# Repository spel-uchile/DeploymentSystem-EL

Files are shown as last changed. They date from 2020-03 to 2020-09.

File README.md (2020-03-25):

# DeploymentSystem-EL
Proyecto de curso EL. Diseño de sistema de despliegue

#### Parte eléctrica
 - Diseñar una nueva placa con un micro más pequeño y utilizando el espacio en los InterStage.
 - Revisar documentacion de Pinout de Stack (https://docs.google.com/spreadsheets/d/16q0HoTVAfZYG_5lE80G09ZOd-HxBMbC0y2KJIxqkWWU/edit#gid=0).
 - Instrucciones con comandos. 
 
#### Parte Mecánica
 - Revisar articulaciones en CAD (Carpeta general de CAD: https://drive.google.com/drive/u/0/folders/1X1Ea6DyqA-4cPEp2hvyv38Jz5EprBwpk).
   "NO MODIFICAR DIRECTAMENTE"
 - Leer CubesatRev 13 especificaciones de diseños (Tolerancias de diseños, dimensiones maximas de extrucción, estandar de dimensión). https://www.cubesat.org/resources.
 - Exportar las caras de los InterStage a DXF para el diseño del Board.
 - Crear articulaciones en los paneles.

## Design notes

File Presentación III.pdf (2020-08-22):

# SPEL: Deployment System

Alumnos: | Diego Benavides
| Javiera Chasco
Profesor Guía: | Elías Obreque

EL4030-1: Seminario de Diseño e Innovación
Facultad de Ciencias Físicas y Matemáticas, Universidad de Chile

# Agenda

- Presentación del problema.
- Tareas asignadas.
- Labores realizadas.
- Estado actual.
- Aprendizajes y próximos pasos.

# Presentación del problema

- La meta del presente trabajo es lograr implementar un circuito eléctrico que sea capaz de activar un sistema de despliegue de los paneles de protección lumínica y radiación del nanosatèlite PlantSat.
- Para ello, se le hace entrega al equipo de trabajo un circuito base que ya es capaz de realizar dicha acción, el cual se puede apreciar en la figura 1.

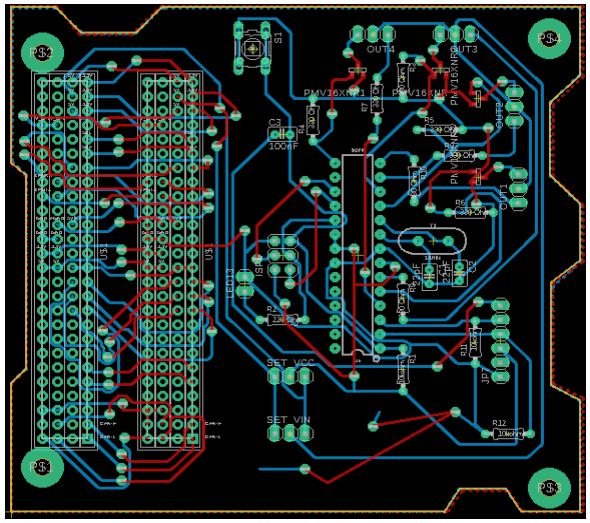
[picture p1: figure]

Figura 1: Placa original del sistema de despliegue.

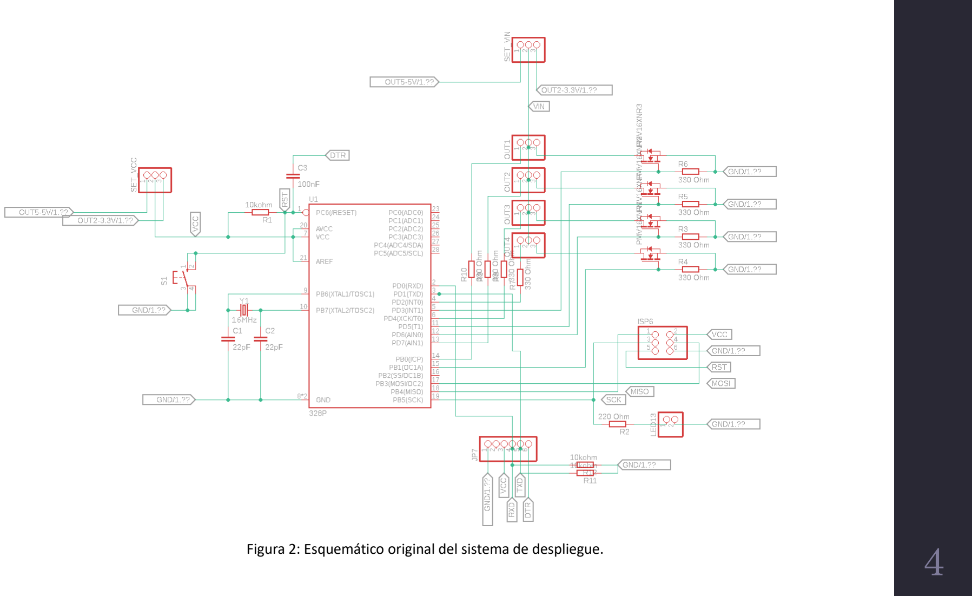
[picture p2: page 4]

Figura 2: Esquemático original del sistema de despliegue.

# Tareas eléctricas designadas

- Realizar una división del circuito original en cuatro subcircuitos.
- Definir un esquema de interconexión entre los subcircuitos y el protocolo de comunicación.
- Buscar o confeccionar componentes SMD para todos los componentes eléctricos del circuito base.
- Rutear los subcircuitos de acuerdo a los estándares de fabricación y recomendaciones de miembros del laboratorio con experiencia previa.
- Revisión y depuración de los esquemáticos y boards para cotizar la fabricación de estos.
- Programar Instrucciones para el funcionamiento de los circuitos.

# Tareas mecánicas asignadas

- Familiarizarse con las especificaciones de diseño descritas en CubesatRev 13.
- Crear soporte para los paneles de despliegue.
- Apoyar en las labores de diseño del esquemático y del board.
- Modificar las placas según necesidad de diseño.
- Crear soporte para montar una cámara en la estructura principal del nanosatélite.

# Especificaciones de diseño del CubeSat

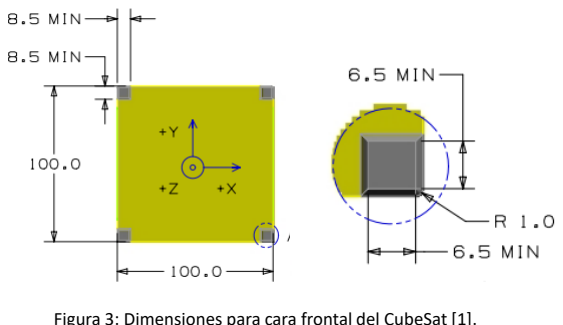
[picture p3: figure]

Figura 3: Dimensiones para cara frontal del CubeSat [1].

Para un CubeSat3U:

- Para la estructura se sugiere utilizar 4 aleaciones de aluminio.
- La masa no debe superar los 4 kg.
- Sus dimensiones deben ser 10x10x34.5 cm³
- Ningún componente puede exceder los 6.5 mm normal a la superficie.
- La tolerancia es ±0.1.

# Especificaciones de diseño del CubeSat

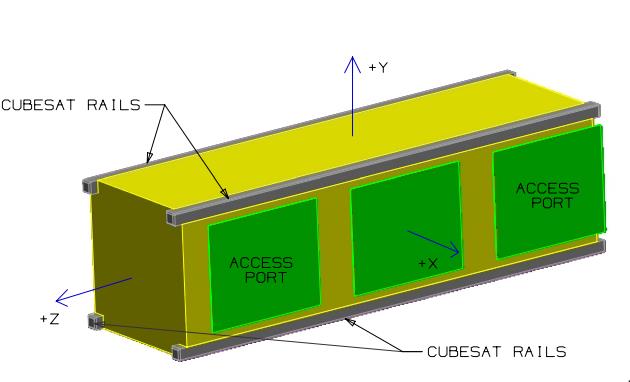
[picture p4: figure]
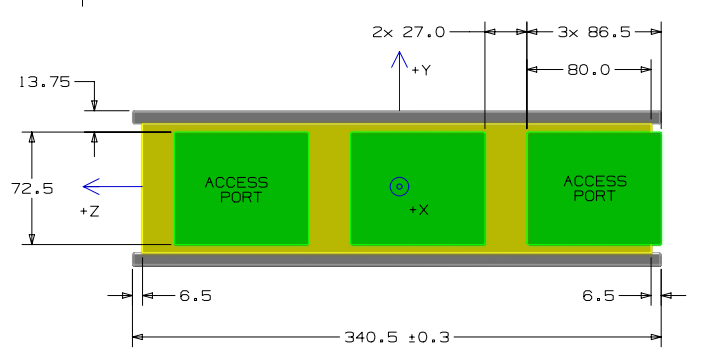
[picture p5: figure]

Figura 4: Dimensiones para cara lateral y vista completa del CubeSat [1].

# Especificaciones de diseño de las PCB

Interstage tipo A

Figura 5: Dimensiones interstage tipo A.

# Especificaciones de diseño de las PCB

Interstage tipo B1

10 Figura 6: Dimensiones interstage tipo B1.

# Especificaciones de diseño de las PCB

Interstage tipo B2

11 Figura 7: Dimensiones interstage tipo B2.

# Especificaciones de diseño de las PCB

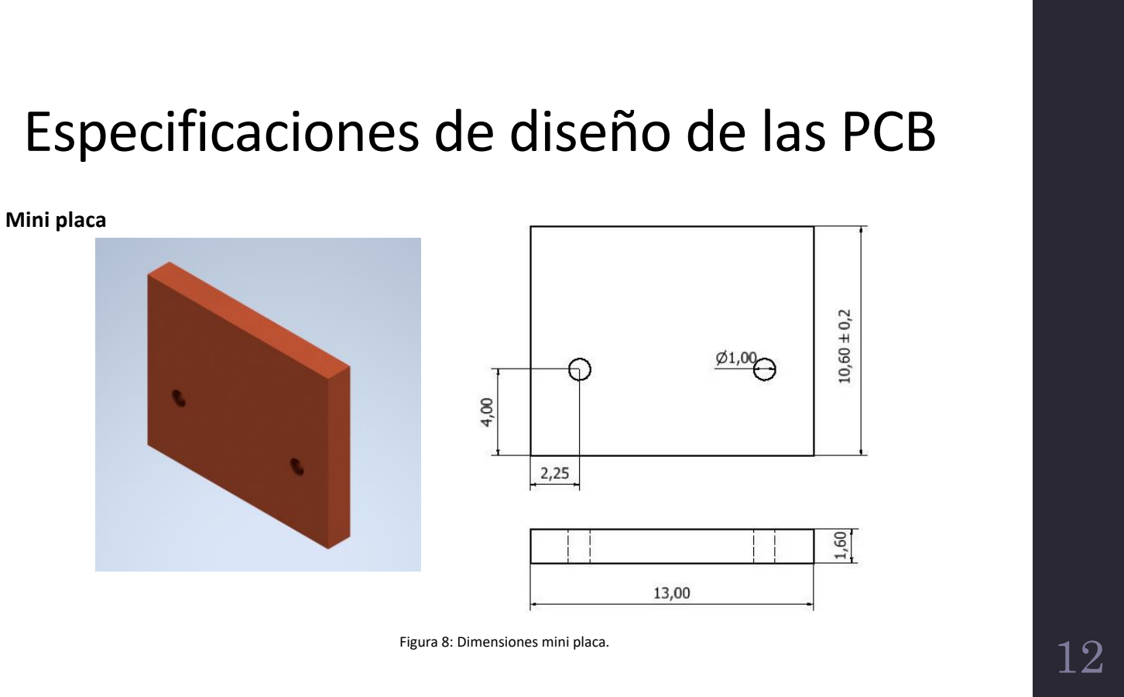
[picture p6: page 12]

Mini placa

12 Figura 8: Dimensiones mini placa.

# Soporte para paneles de despliegue

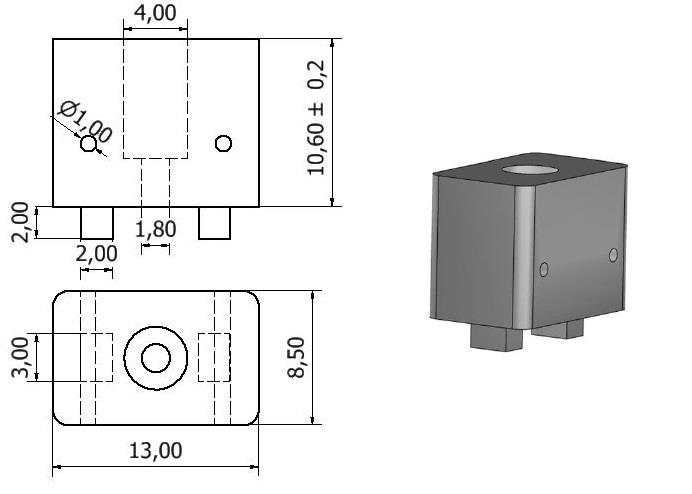
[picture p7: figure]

13 Figura 9: Dimensiones soporte para paneles solares.

# Soporte para cámara

- Se desea diseñar un soporte para un módulo de cámara Raspberry Pi V2.
- El soporte debe ocupar el espacio libre en la estructura, tratando de ser lo menos invasivo posible.

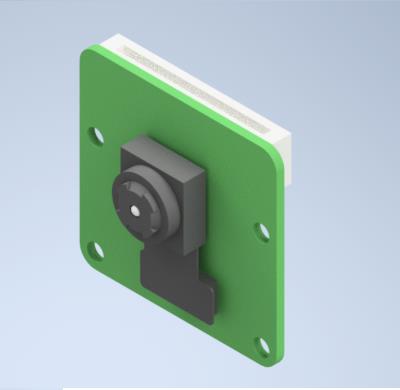
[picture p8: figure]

Figura 10 : Módulo de cámara Raspberry Pi V2.

# Soporte para cámara

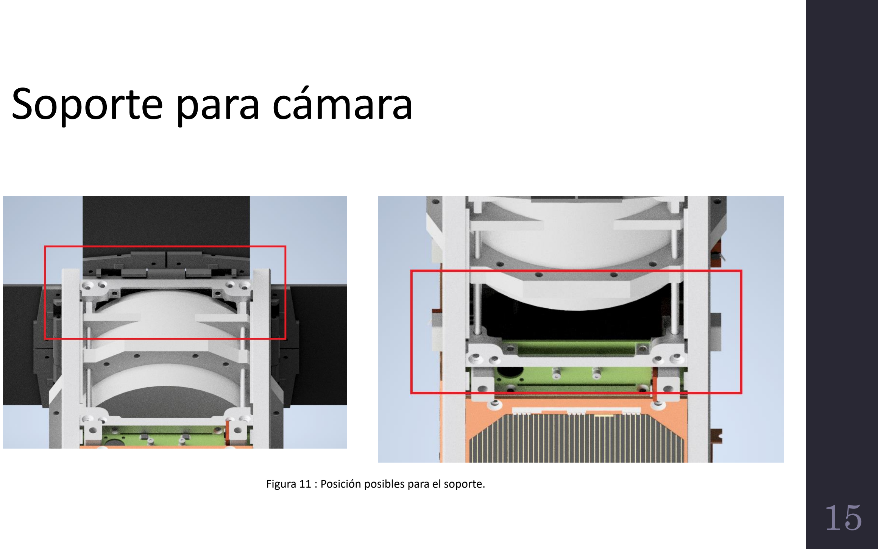
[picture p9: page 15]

Figura 11 : Posición posibles para el soporte.

# Soporte para cámara

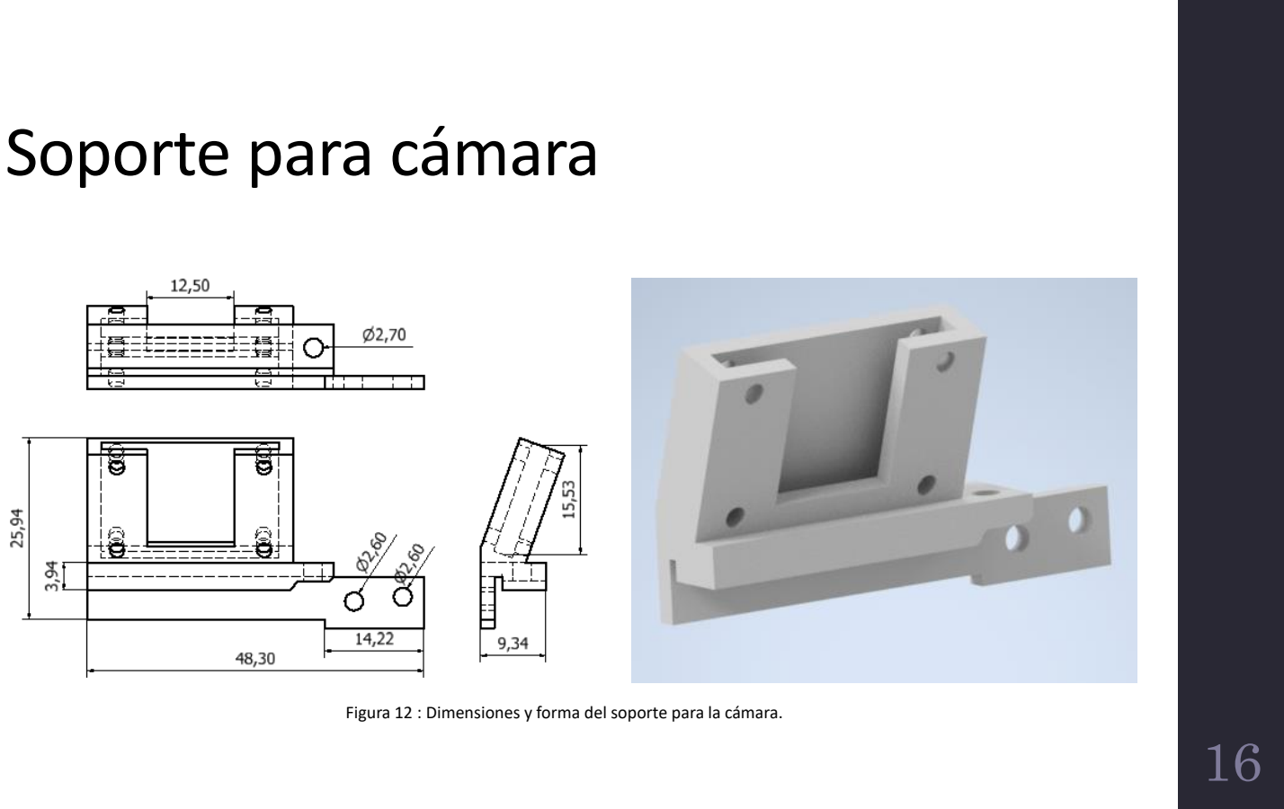
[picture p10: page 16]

Figura 12 : Dimensiones y forma del soporte para la cámara.

# Soporte para cámara

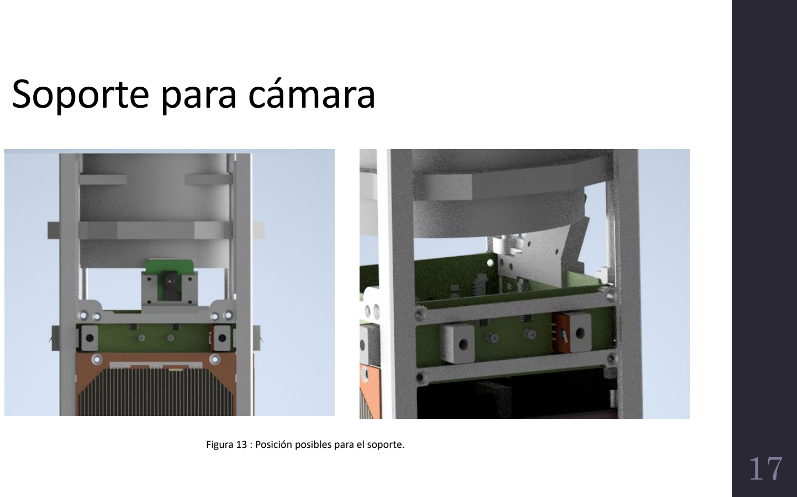
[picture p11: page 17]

Figura 13 : Posición posibles para el soporte.

# Ubicación de las placas

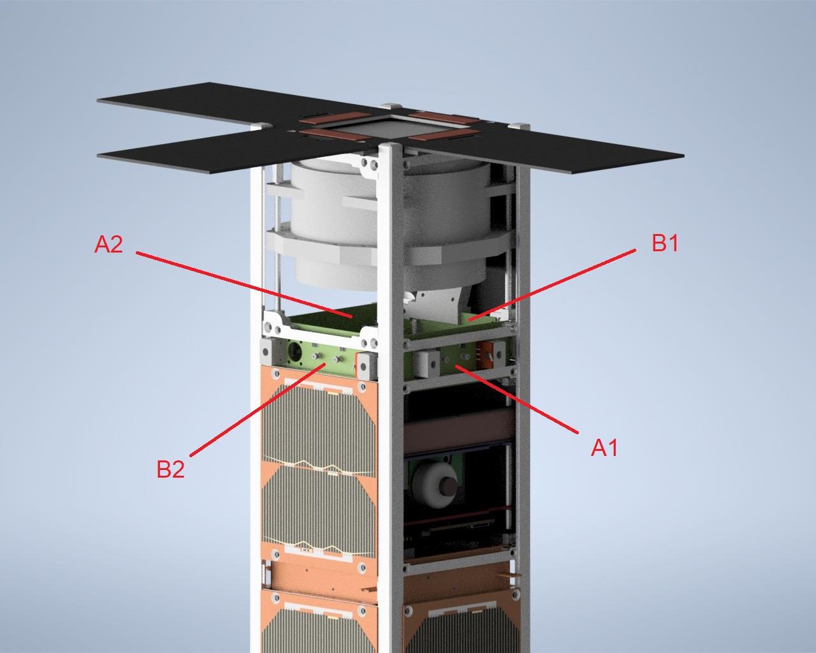
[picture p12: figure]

18 Figura 14: Vista 3D de PlantSat

# Esquema de conexión eléctrica propuesto

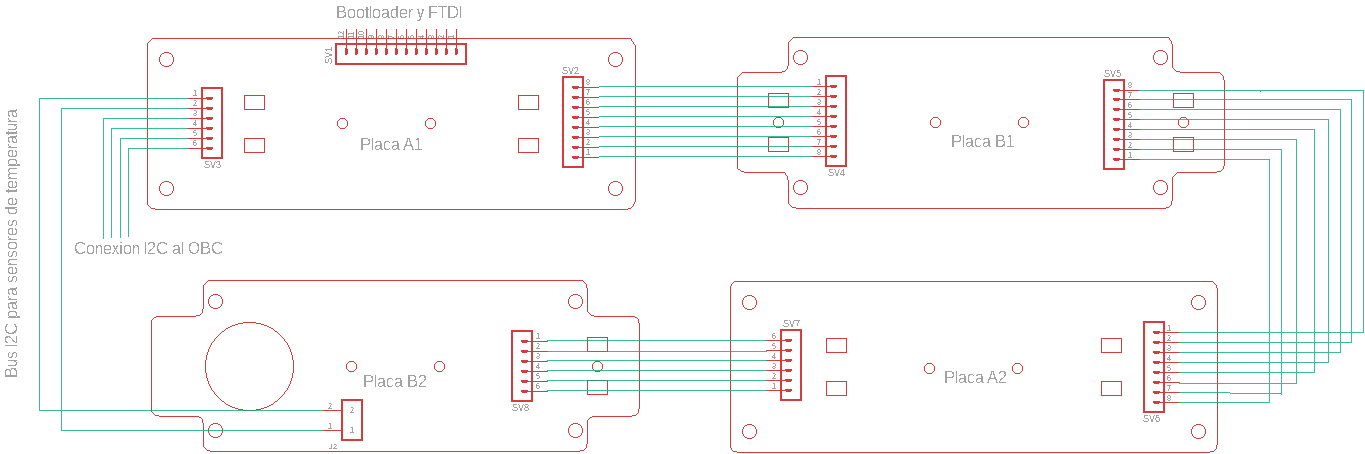
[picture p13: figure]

19 Figura 15: Esquemàtico general del circuito propuesto.

# Esquema de conexión eléctrica propuesto

Placa principal: A1

- Corresponde a la placa central del sistema de despliegue, pues de este lugar se envían desde el microcontrolador (ATmega 328p) las ordenes de activación del sistema de despliegue para cada placa, y donde también se procesan las lecturas de medición de temperatura de estas. Por simplicidad, tanto la placa como los dispositivos que se encuentran ubicados en ella son alimentados con un voltaje continuo de 5V.
- Cuenta con un microcontrolador, dos sensores de temperatura, un interruptor de contacto, y el mosfet para activar el sistema de despliegue de un panel.

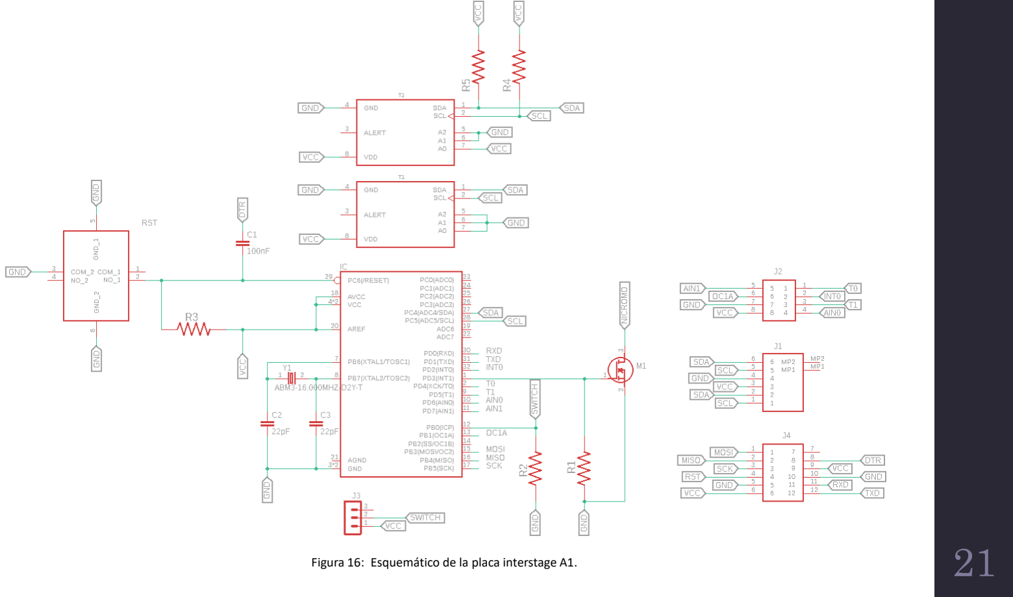
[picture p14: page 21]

Figura 16: Esquemático de la placa interstage A1. | 21

# Esquema de conexión eléctrica propuesto

Placas secundarias: B1, A2 y B2

- Son placas que reciben ordenes desde la principal, son capaces de activar el sistema de despliegue de sus paneles asociados y de registrar la temperatura fuera del satelite.
- A diferencia de la principal, cada una de ellas está compuesta por dos sensores de temperatura, un interruptor de contacto, y un mosfet para activar el sistema de despliegue de un panel.

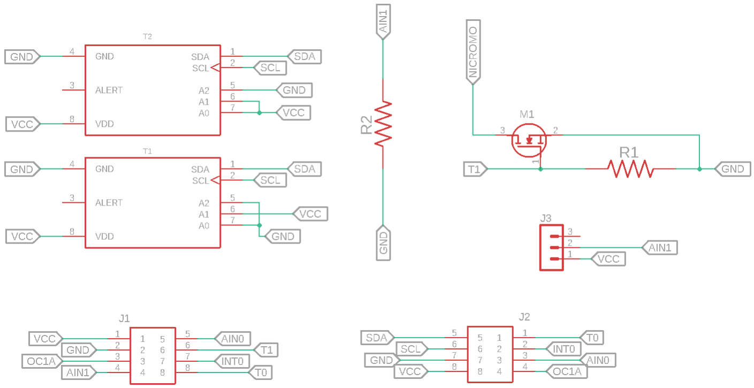
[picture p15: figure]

Figura 17: Esquemático de la placa interstage B1. | 23

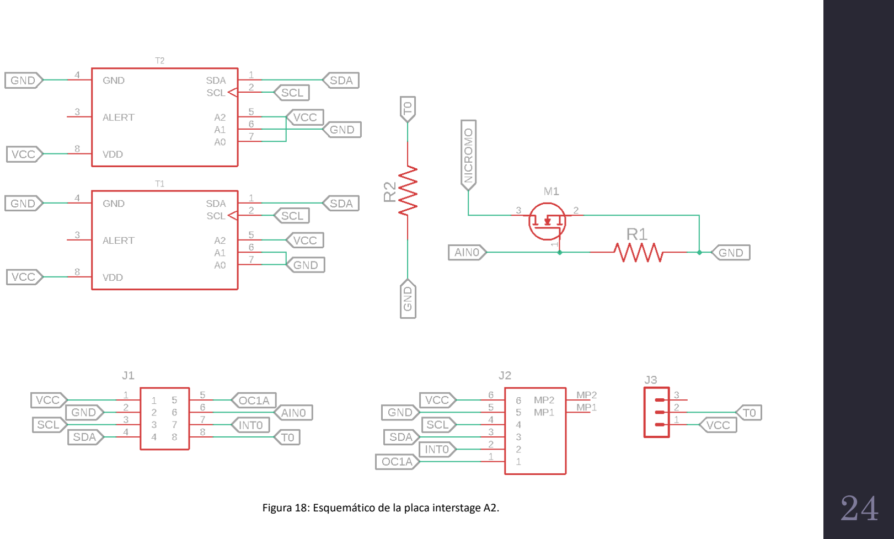
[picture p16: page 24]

Figura 18: Esquemático de la placa interstage A2. | 24

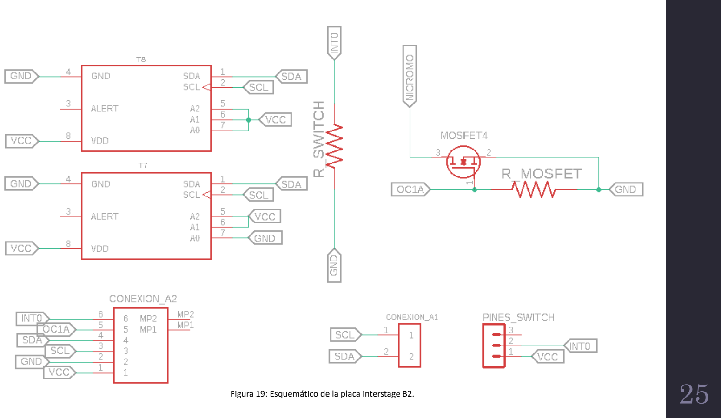
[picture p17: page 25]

Figura 19: Esquemático de la placa interstage B2. | 25

# Esquema de conexión eléctrica propuesto

PMinipla

- Es una pequeña placa de cobre cuya única función es contener al switch que detecta la apertura de los paneles de despliegue.
- Cuenta con 3 pines para conectarse perpendicularmente a cada una de las placas anteriormente mencionadas.

# Esquemáticos realizados

Miniplaca para switch TH:

- Es una pequeña placa de cobre cuya única función es contener al switch que detecta la apertura de los paneles de despliegue.
- Cuenta con 3 pines para conectarse perpendicularmente a cada una de las placas anteriormente mencionadas.

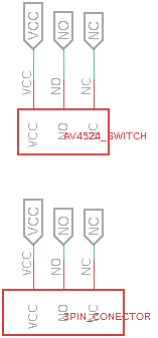
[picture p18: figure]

Figura 13: Esquemático de la miniplaca (opcion 1). | 28

# Esquemáticos realizados

Miniplaca para switch SMD:

- Es una segunda versión de la misma placa anterior, cuya única diferencia es que el switch es de un tamaño considerablemente menor y es soldado superficialmente.

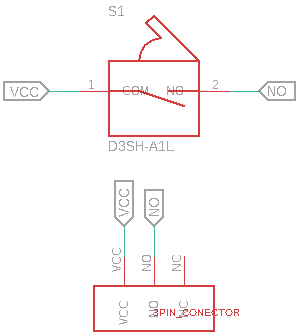
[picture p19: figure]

Figura 14: Esquemático de la miniplaca (opcion 2). | 30

# Placas obtenidas

Interstage tipo A1

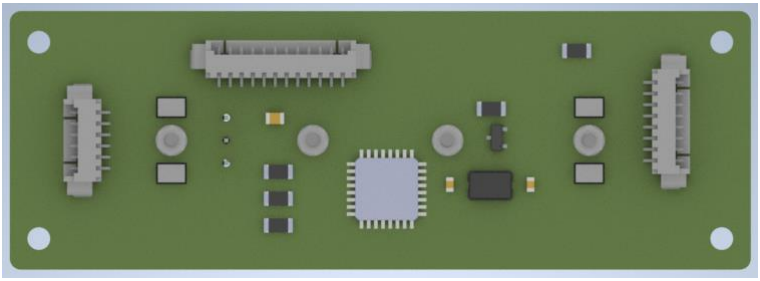
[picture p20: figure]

Figura 15: Placa interstage tipo A1.

# Placas obtenidas

Interstage tipo B1

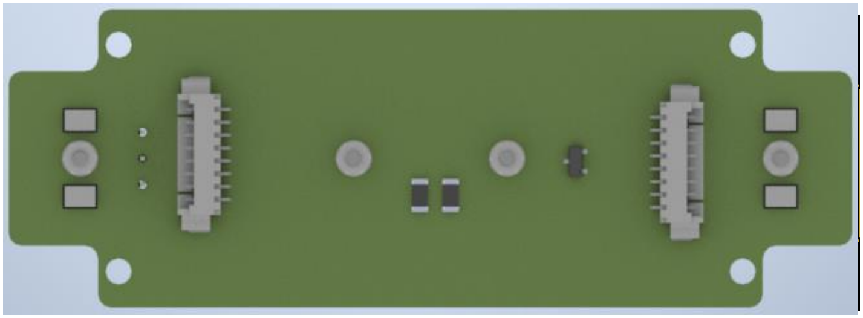
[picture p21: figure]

32 Figura 16: Placa interstage tipo B1.

# Placas obtenidas

Interstage tipo A2

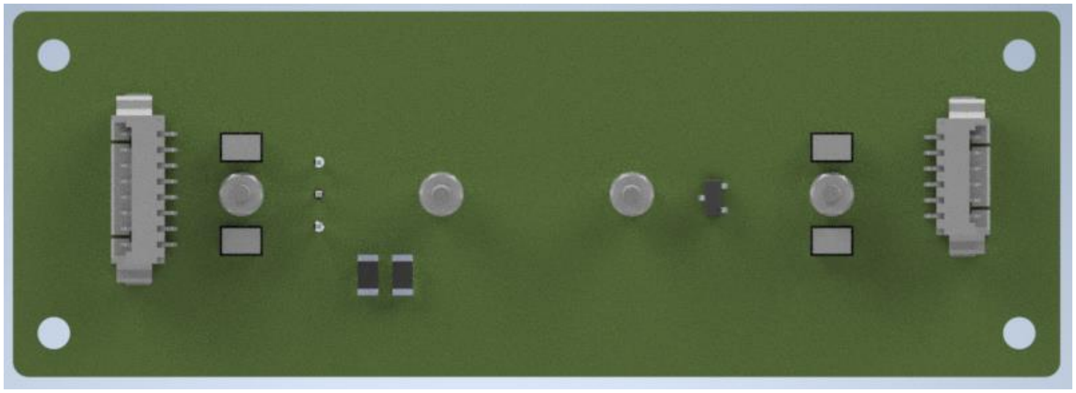
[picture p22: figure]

33 Figura 17: Placa interstage tipo A2.

# Placas obtenidas

Interstage tipo B2

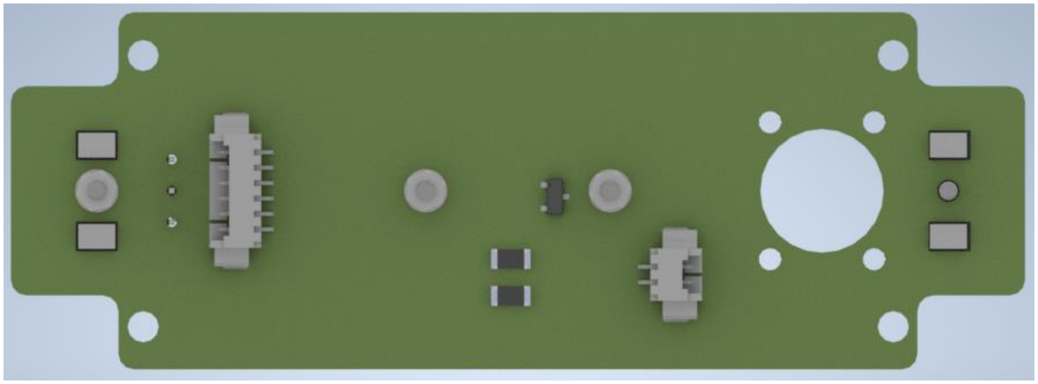
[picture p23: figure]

34 Figura 18: Placa interstage tipo B2.

# Placas obtenidas

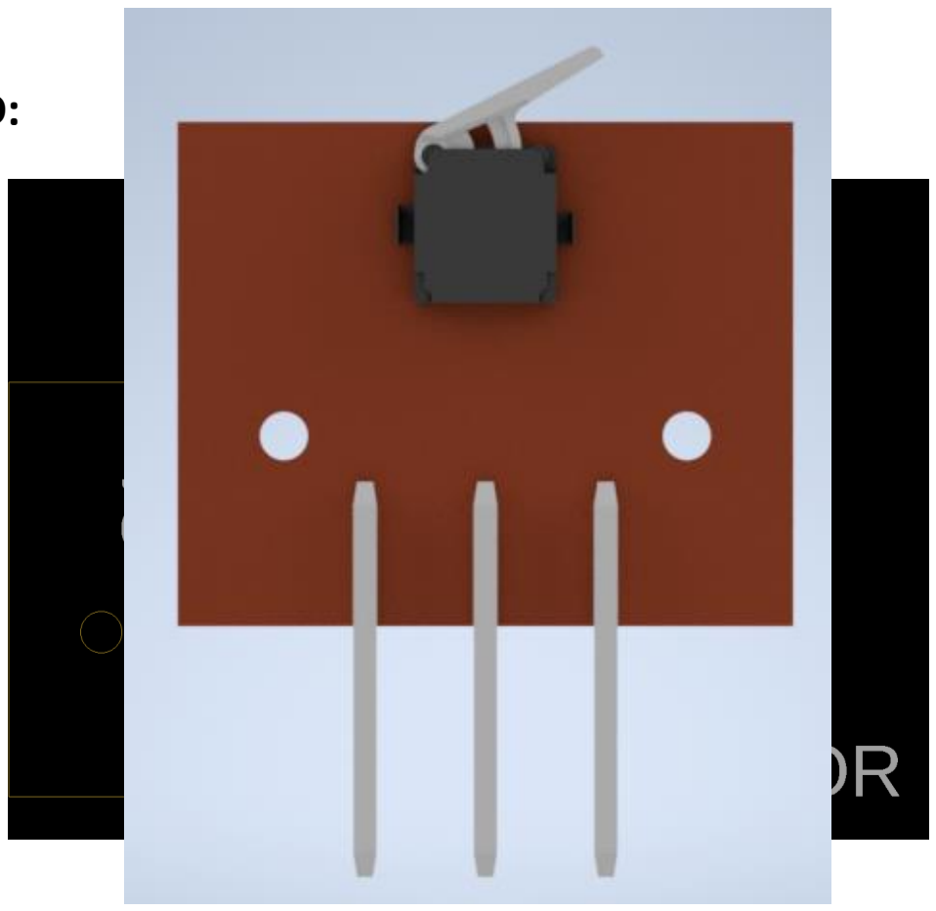
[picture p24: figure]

Miniplaca para switch SMD:

35 Figura 20: Miniplaca para switch tipo SMD.

# Aprendizajes obtenidos

- Conocer las especificaciones técnicas de diseño que debe tener un CubeSat.
- Comprender a grandes rasgos el proceso que se debe desarrollar para desplegar los paneles de un nanosatélite.
- Familiarización con las diversas herramientas que ofrece Inventor.
- Familiarización con la importación de esquemáticos, footprints y librerías de Eagle en general.
- Afinación del proceso de búsqueda de componentes electrónicos con EDA/CAD en el mercado.
- Comprensión del funcionamiento de las capas en Eagle. Particularmente, la modificación de la capa que modela las dimensiones de una PCB.
- Familiarización con las otras herramientas de diseño de PCB que ofrece Eagle, como lo son: polygon, ratsnest e isolate.
- Documentación de los componentes utilizados para optimizar el tiempo de búsqueda en sesiones de trabajo futuras.

# Dificultades encontradas

- Definir pines del Atmega en donde se conectarán las señales de los sensores de temperatura (Comunicación SPI). Se optó por comunicación I2C.
- Comprender el uso y las conexiones del Nicromo.
- Definir qué tipo de interruptor se utilizará para detectar la apertura y cierre de los paneles de despliegue en cada interstage.
- Definir ubicación de los interruptores anteriores.
- Creación de esquemáticos y librerías.

# Próximos pasos

- Mandar a fabricar las placas.
- Soldar los componentes SMD y TH.
- Definir si se usará el switch de contacto SMD o TH.
- Testear y verificar el correcto funcionamiento de los dispositivos.
- Escribir el código para programar el microcontrolador y realizar testeos finales.
- Interés en continuar en el proyecto para realizar mejores versiones en base a los resultados de las pruebas anteriores.

# Referencias

[1] CDS, CubeSat Design Specification, Rev. 13, California Polytechnic State University, 2015.
[2] Benavides, D., Chasco, J., Obreque E., (10 de julio de 2020). SPEL:
DeploymentSystem-EL. | https://github.com/spel-uchile/DeploymentSystem-EL
[3] Becerra, A. (08 de julio de 2020). Diseño de Placas [Webinar]. Space and Planetary Exploration Laboratory (SPEL).

# SPEL: Deployment System

Alumnos: | Diego Benavides
| Javiera Chasco
Profesor Guía: | Elías Obreque

EL4030-1: Seminario de Diseño e Innovación
Facultad de Ciencias Físicas y Matemáticas, Universidad de Chile

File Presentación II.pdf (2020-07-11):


# SPEL: Deployment System

Alumnos: | Diego Benavides
| Javiera Chasco
Profesor Guía: | Elías Obreque

EL4030-1: Seminario de Diseño e Innovación
Facultad de Ciencias Físicas y Matemáticas, Universidad de Chile

# Agenda


- Objetivos.
- Tareas asignadas.
- Especificaciones de diseño.
- Resultados obtenidos y estado actual.
- Aprendizajes y próximos pasos.

# Objetivos

Objetivo general:

- Se desea diseñar, construir y programar el circuito eléctrico involucrado en el despliegue de paneles del nanosatélite PlantSat.

Objetivos específicos:

- Estudiar las especificaciones técnicas del CubeSat.
- Descomponer circuito existente y reubicar componentes en distintas placas.
- Familiarizarse con Eagle e Inventor.

# Tareas eléctricas designadas

- Revisar documentación de pinout de stack.
- Rediseño de la placa original, dividiendola en cuatro secciones/placas.
- Buscar o confeccionar equivalentes SMD de algunos dispositivos: microcontrolador, botones de siwtch, mosfet, etc.
- Realizar esquema de interconexion entre las placas y definir el tipo de canal de comunicación de los sensores de temperatura.
- Revisión de la forma y demensiones de las rutas de acuerdo a los estandares de fabricación y recomendaciones varias de miembros del laboratorio con experiencia previa.
- Programar Instrucciones para el microcontrolador.

# Tareas mecánicas asignadas

- Revisar articulaciones en CAD.
- Leer CubesatRev 13 especificaciones de diseños (Tolerancias de diseños, dimensiones máximas de extracción, estándar de dimensión).
- Exportar las caras de los InterStage a DXF para el diseño del Board.
- Crear articulaciones en los paneles.
- Crear soporte para los paneles de despliegue.
- Apoyar en las labores de diseño del board.

# Especificaciones de diseño del CubeSat


Figura 1: Poly Picosatellite Orbital Deployer [1].

¿Qué son los CubeSats?

- Son nanosatélites que cumplen con los estándares descritos en el CubeSat Design Specification.
- Su forma más simple y estándar en un cubo de 10x10x11.35 cm³
, llamado CubeSat 1U.
- PlanSat es un nanosatélite que consta de 3 unidades.
- El mecanismo de despliegue de los CubeSat es el P-POD.

# Especificaciones de diseño del CubeSat


Figura 2: Dimensiones para cara frontal del CubeSat [1].

Para un CubeSat3U:

- Para la estructura se sugiere utilizar 4 aleaciones de aluminio.
- La masa no debe superar los 4 kg.
- Sus dimensiones deben ser 10x10x34.5 cm³
- Ningún componente puede exceder los 6.5 mm normal a la superficie.
- La tolerancia es ±0.1.

# Especificaciones de diseño del CubeSat


Figura 3: Dimensiones para cara lateral y vista completa del CubeSat [1].

# Especificaciones de diseño de las PCB

- Se desea reducir de tamaño el circuito original.
- Para ello, se quita el stack de la placa, para
dejar | aislado | el | circuito | del
microcontrolador.
- Luego, el circuito resultante se separa en 4 subcircuitos, los cuales se ubicarán en los interstage del nanosatélite.


Figura 4: Placa original del deployment system.

# Especificaciones de diseño de las PCB


Interstage tipo A

10 Figura 5: Dimensiones interstage tipo A.

# Especificaciones de diseño de las PCB


Interstage tipo B1

11 Figura 6: Dimensiones interstage tipo B1.

# Especificaciones de diseño de las PCB


Interstage tipo B2

12 Figura 7: Dimensiones interstage tipo B2.

# Especificaciones de diseño de las PCB

Mini placa


13 Figura 8: Dimensiones mini placa.

# Soporte para paneles de despliegue


14 Figura 9: Dimensiones soporte para paneles solares.

# Esquemáticos realizados

Interstage A1:

- Placa principal. Contiene un microcontrolador (con su botón de reset), dos sensores de temperatura, un mosfet (que controla la corriente del nicromo) y un switch (que detecta la apertura de los paneles).
- Adicionalmente esta placa cuenta con 3 picoblade molex, los cuales permiten intercambiar la información de esta placa con el puerto de programación, con la placa A2 y con la placa B1, respectivamente.
- Se utiliza conexión i2C estandar para el ftdi y el bootloader (programación del microcontrolador).
- Similarmente, se usa conexión i2C estándar para el intercambio de información entre los sensores de las otras placas y el microcontrolador.


Figura 10; Esquemático de la placa interstage A1. | 16

# Esquemáticos realizados

Interstage B1:

- Placa secundaria, contiene dos sensores de temperatura y un sensor de contacto (switch)
- Cuenta con 2 picoblade molex, para intercambiar información de los sensores y el switch directamente con la placa del microcontrolador, y para transportar la información proveniente de las demás placas también hacia el microcontrolador de la placa A1.


Figura 11: Esquemático de la placa interstage B1. | 18

# Esquemáticos realizados

Interstage A2:

- Placa secundaria, contiene los mismos componentes que la placa anterior, con la salvedad de que la forma de la placa es idéntica a la principal (A1).


Figura 12: Esquemático de la placa interstage A2. | 20

# Esquemáticos realizados

Interstage B2:

- Placa secundaria, además de contener los mismos componentes que las dos anteriores, esta incluye un vaciado para ajustarse al diseño físico que tiene el nanosatélite. Luego, su espacio es más reducido, por lo que es la placa que menos señales transporta.


Figura 13: Esquemático de la placa interstage B2. | 22

# Esquemáticos realizados

Miniplaca para switch TH:

- Es una pequeña placa de cobre cuya unica función es contener al switch que detecta la apertura de los paneles de despliegue.
- Cuenta con 3 pines para conectarse perpendicularmente a cada una de las placas anteriormente mencionadas.
- Switch de tamaño significativamente mayor que su contraparte de soldadura superficial.
- Modelo del switch no incluye esquemático ni footprint, por lo que se diseña tomando como referencia la hoja de datos del fabricante.


Figura 13: Esquemático de la miniplaca (opcion 1). | 24

# Esquemáticos realizados

Miniplaca para switch SMD:

- Es una segunda versión de la misma placa anterior, cuya única diferencia es que el switch es de un tamaño considerablemente menor y es soldado superficialmente.


Figura 14: Esquemático de la miniplaca (opcion 2). | 26

# Placas obtenidas

Interstage tipo A1


27 Figura 15: Placa interstage tipo A1.

# Placas obtenidas

Interstage tipo B1


28 Figura 16: Placa interstage tipo B1.

# Placas obtenidas

Interstage tipo A2


29 Figura 17: Placa interstage tipo A2.

# Placas obtenidas

Interstage tipo B2


30 Figura 18: Placa interstage tipo B2.

# Placas obtenidas

Miniplaca para switch TH:

31 Figura 19: Miniplaca para switch tipo TH.

# Placas obtenidas


Miniplaca para switch SMD:

32 Figura 20: Miniplaca para switch tipo SMD.

# Aprendizajes obtenidos

- Conocer las especificaciones técnicas de diseño que debe tener un cubesat.
- Comprender a grandes rasgos el proceso que se debe desarrollar para desplegar los paneles de un nanosatélite.
- Familiarización con las diversas herramientas que ofrece Inventor.
- Familiarización con la importación de esquemáticos, footprints y librerías de Eagle en general.
- Afinación del proceso de búsqueda de componentes electrónicos con EDA/CAD en el mercado.
- Comprensión del funcionamiento de las capas en Eagle. Particularmente, la modificación de la capa que modela las dimensiones de una PCB.
- Familiarización con las otras herramientas de diseño de PCB que ofrece Eagle, como lo son: polygon, ratsnest e isolate.
- Documentación de los componentes utilizados para optimizar el tiempo de búsqueda en sesiones de trabajo futuras.

# Dificultades encontradas

- Definir pines del Atmega en donde se conectarán las señales de los sensores de temperatura (Comunicación SPI). Se optó por comunicación I2C.
- Comprender el uso y las conexiones del Nicromo.
- Definir qué tipo de interruptor se utilizará para detectar la apertura y cierre de los paneles de despliegue en cada interstage.
- Definir ubicación de los interruptores anteriores.
- Creación de esquemáticos y librerías.

# Próximos pasos

- Mandar a fabricar las placas.
- Soldar los componentes SMD y TH.
- Definir si se usará el switch de contacto SMD o TH.
- Testear y verificar el correcto funcionamiento de los dispositivos.
- Escribir el código para programar el microcontrolador y realizar testeos finales.
- Interés en continuar en el proyecto para realizar mejores versiones en base a los resultados de las pruebas anteriores.

# Referencias

[1] CDS, CubeSat Design Specification, Rev. 13, California Polytechnic State University, 2015.
[2] Benavides, D., Chasco, J., Obreque E., (10 de julio de 2020). SPEL:
DeploymentSystem-EL. | https://github.com/spel-uchile/DeploymentSystem-EL
[3] Becerra, A. (08 de julio de 2020). Diseño de Placas [Webinar]. Space and Planetary Exploration Laboratory (SPEL).

# SPEL: Deployment System

Alumnos: | Diego Benavides
| Javiera Chasco
Profesor Guía: | Elías Obreque

EL4030-1: Seminario de Diseño e Innovación
Facultad de Ciencias Físicas y Matemáticas, Universidad de Chile

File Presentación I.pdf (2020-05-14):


# SPEL: Deployment System

Alumnos: | Diego Benavides
| Javiera Chasco
Profesor Guía: | Elías Obreque

EL4030-1: Seminario de Diseño e Innovación
Facultad de Ciencias Físicas y Matemáticas, Universidad de Chile

Agenda • Objetivos. • Tareas mecánicas asignadas


- Especificaciones de diseño del CubeSat

- Tareas eléctricas asignadas

- Especificaciones de diseño de las PCB

- Resultados obtenidos

y estado actual

- Aprendizajes

- Próximos pasos

# Objetivos

Objetivo general:

- Se desea diseñar, construir y programar el circuito eléctrico involucrado en el despliegue de paneles del nanosatélite PlantSat.

Objetivos específicos:

- Estudiar las especificaciones técnicas del CubeSat.
- Descomponer circuito existente y reubicar componentes en distintas placas.
- Familiarizarse con Eagle e Inventor.

# Tareas mecánicas asignadas

- Revisar articulaciones en CAD.
- Leer CubesatRev 13 especificaciones de diseños (Tolerancias de diseños, dimensiones máximas de extracción, estándar de dimensión).
- Exportar las caras de los InterStage a DXF para el diseño del Board.
- Crear articulaciones en los paneles

# Especificaciones técnicas del CubeSat

¿Qué son los CubeSats?

- Son nanosatélites que cumplen con los estándares descritos en el CubeSat Design Specification.
- Su forma más simple y estándar en un cubo de 10x10x11.35 cm³
, llamado CubeSat 1U.
- PlanSat es un nanosatélite que consta de 3 unidades.
- El mecanismo de despliegue de los CubeSat es el P-POD.


Figura 1: Poly Picosatellite Orbital Deployer [1].

# Especificaciones técnicas del CubeSat

Especificaciones mecánicas de diseño de CubeSat 3U

- Define principalmente las tolerancias en las dimensiones, la masa y tipo de material.
- Para la estructura se sugiere utilizar 4 aleaciones de aluminio.
- Para un CubeSat 3U, la masa no debe superar los 4 kg.
- Sus dimensiones deben ser 10x10x34.5 cm³ .
- Ningún componente puede exceder los 6.5 mm normal a la superficie.
- La tolerancia es ±0.1.


Figura 2: Dimensiones para cara frontal del CubeSat [1].

# Especificaciones técnicas del CubeSat

Especificaciones de diseño de CubeSat 3U


Figura 3: Dimensiones para cara lateral y vista completa del CubeSat [1].

# Tareas eléctricas designadas

- Diseñar un board con un microcontrolador mas pequeño, aprovechando el espacio de los interstage del nanosatélite.
- Revisar documentación de pinout de stack.
- Programar Instrucciones para el microcontrolador.

# Especificaciones de diseño de las PCB

- Se desea reducir de tamaño el circuito original.
- Para ello, se quita el stack de la placa, para
dejar | aislado | el | circuito | del
microcontrolador.
- Luego, el circuito resultante se separa en 4 subcircuitos, los cuales se ubicarán en los interstage del nanosatélite.


Figura 4: Placa original del deploymentsystem.

# Especificaciones de diseño de las PCB

Interstage tipo A


10 Figura 4: Dimensiones interstage tipo A.

# Especificaciones de diseño de las PCB

Interstage tipo B1


11 Figura 5: Dimensiones interstage tipo B1.

# Especificaciones de diseño de las PCB

Interstage tipo B2


12 Figura 6: Dimensiones interstage tipo B2.

# Resultados obtenidos

Interstage A1:

- Placa principal, contiene al microcontrolador y todas las terminales necesarias para enviar y recibir las señales de los sensores de las otras placas. Cuenta también con terminales de conexión i2C estándar, conexión a ftdi y a bootloader (programación del microcontrolador).
- Adicionalmente, esta placa debe contener dos sensores de temperatura y 1 sensor de contacto (switch). Aunque estos no han sido implementados aún, pues se requiere conocer de forma mas acaba las terminales donde llegarán dichas señales.


Figura 7: Esquemático de la placa interstage A1. | 14

# Resultados obtenidos

Interstage B1:

- Placa secundaria, contiene dos sensores de temperatura y un sensor de contacto (switch), cuenta con las terminales necesarias para enviar señales al microcontrolador y recibir instrucciones de este. Cuenta también con terminales para transportar la alimentación, tierra y señales de las otras placas.

# Resultados obtenidos


Interstage B1:

Figura 8: Esquemático de la placa interstage B1. | 16

# Resultados obtenidos

Interstage A2:

- Placa secundaria, contiene los mismos componentes que la placa anterior, con la salvedad de que la forma de la placa es idéntica a la principal (A1).

# Resultados obtenidos


Interstage B1:

Figura 9: Esquemático de la placa interstage A2. | 18

# Resultados obtenidos

Interstage B2:

- Placa secundaria, además de contener los mismos componentes que las dos anteriores, esta incluye un vaciado para ajustarse al diseño físico que tiene el nanosatélite. Luego, su espacio es mas reducido, por lo que es la placa que menos señales transporta.


Figura 10: Esquemático de la placa interstage B2. | 20

# Estado actual

Interstage tipo A1


21 Figura 11: Placa interstage tipo A1.

# Estado actual

Interstage tipo B1: Desarrollarlo implica tener lista la placa interstage tipo A2.


22 Figura 12: Placa interstage tipo B1.

# Estado actual

Interstage tipo B2


23 Figura 13: Placa interstage tipo B2.

# Aprendizajes obtenidos

- Conocer las especificaciones técnicas de diseño que debe tener un cubesat.
- Comprender a grandes rasgos el proceso que se debe desarrollar para desplegar los paneles de un nanosatélite.
- Familiarización con las diversas herramientas que ofrece Inventor.
- Familiarización con la importación de esquemáticos, footprints y librerías de Eagle en general.
- Afinación del proceso de búsqueda de componentes electrónicos con EDA/CAD en el mercado.
- Comprensión del funcionamiento de las capas en Eagle. Particularmente, la modificación de la capa que modela las dimensiones de una PCB.
- Familiarización con las otras herramientas de diseño de PCB que ofrece Eagle, como lo son: polygon, ratsnest e isolate.
- Documentación de los componentes utilizados para optimizar el tiempo de búsqueda en sesiones de trabajo futuras.

# Próximos Pasos

- Definir los pines del Atmega en donde se conectarán las señales de los sensores de temperatura.
- Definir el modo de conexión entre las señales de los sensores entre la parte Top y Bottom de cada interstage, considerando el uso del Nicromo.
- Decidir si usar conexiones de alimentación y tierra en picoblades separados.
- Investigar sobre como funciona el Nicromo.
- Definir que tipo de interruptor se utilizará para detectar la apertura y cierre de los paneles solares en cada interstage.
- Definir ubicación de los interruptores anteriores.

# Bibliografía

[1] CDS, CubeSat Design Specification, Rev. 13, California Polytechnic State University, 2015.

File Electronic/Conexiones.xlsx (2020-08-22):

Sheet: Atmega
PIN | Componente asociado
ICP | Interruptor de contacto placa A1
INT1 | Mosfet placa A1
AIN1 | Interruptor de contacto placa B1
T1 | Mosfet placa B1
T0 | Interruptor de contacto placa A2
AIN0 | Mosfet A2
INT0 | Interruptor de contacto plaa B2
OC1A | Mosfet B2

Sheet: Placa A1
Picoblade izquierdo | Picoblade derecho
SCL | VCC
SDA | GND
VCC | OC1A
GND | AIN1
SCL | AIN0
SDA | T1
- | INT0
- | T0

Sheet: Placa B1
Picoblade izquierdo | Picoblade derecho
VCC | VCC
GND | GND
OC1A | SCL
AIN1 | SDA
AIN0 | OC1A
T1 | AIN0
INT0 | INT0
T0 | T0

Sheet: Placa A2
Picoblade izquierdo | Picoblade derecho
VCC | VCC
GND | GND
SCL | SCL
SDA | SDA
OC1A | INT0
AIN0 | OC1A
INT0 | -
T0 | -

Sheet: Placa B2
Picoblade izquierdo | Picoblade derecho
VCC | VCC
GND | GND
SCL | SCL
SDA | SDA
INT0 | -
OC1A | -
- | -
- | -

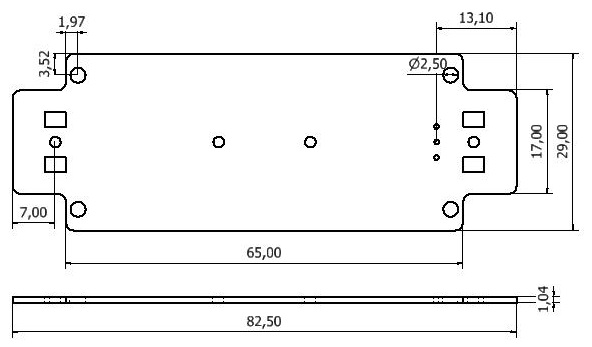
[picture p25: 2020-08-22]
Mechanic/DXF placas/Dimensiones/Placa B1.jpg

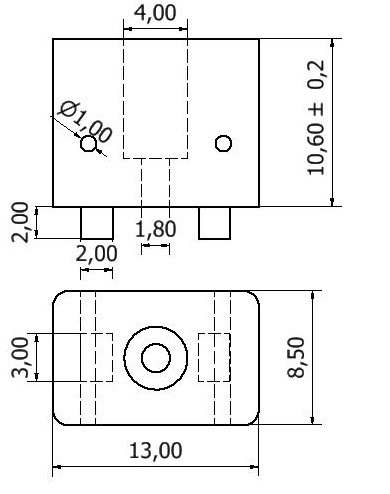
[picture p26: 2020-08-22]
Mechanic/DXF placas/Dimensiones/Soporte Paneles.jpg

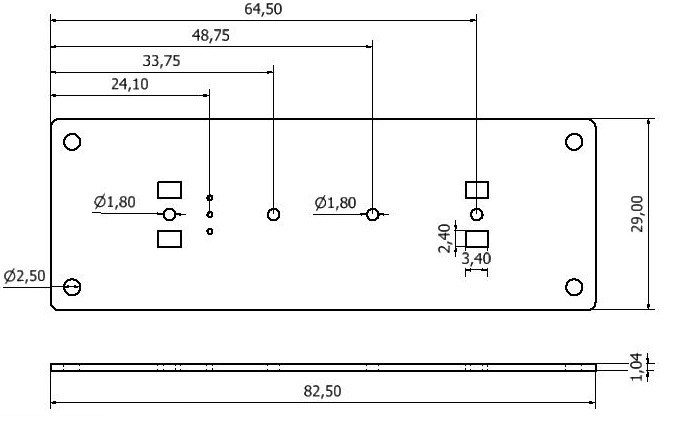
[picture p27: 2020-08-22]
Mechanic/DXF placas/Dimensiones/Placa A.jpg

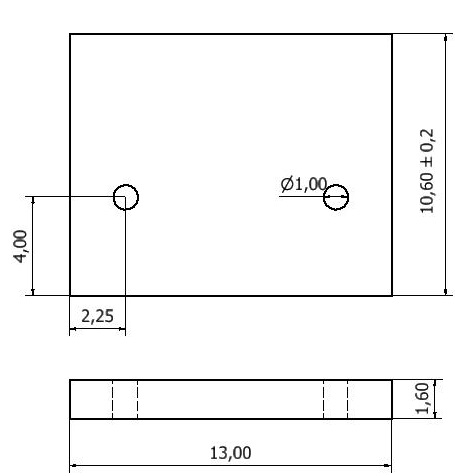
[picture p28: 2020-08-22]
Mechanic/DXF placas/Dimensiones/Placa Cobre.jpg

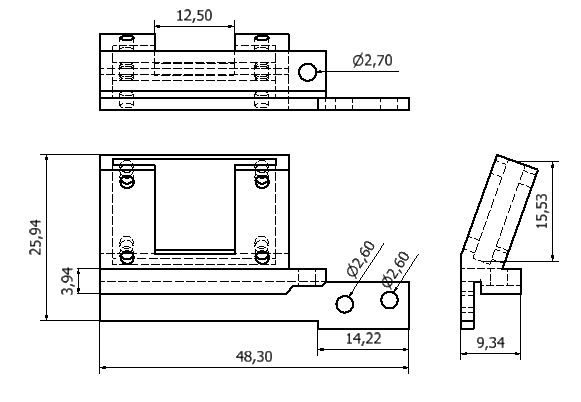
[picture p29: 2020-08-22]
Mechanic/DXF placas/Dimensiones/Soporte Cámara.PNG

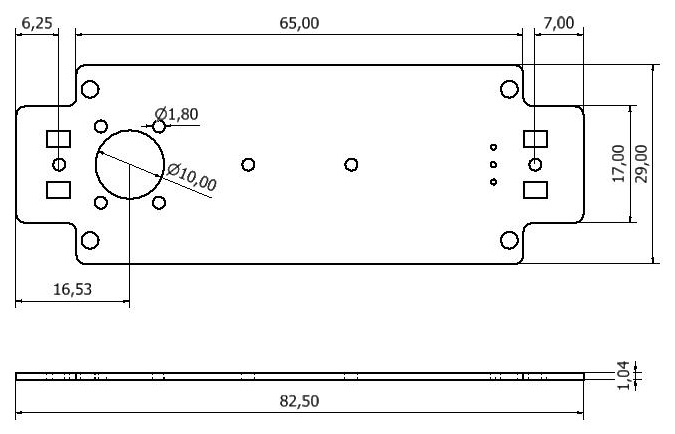
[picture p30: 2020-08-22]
Mechanic/DXF placas/Dimensiones/Placa B2.jpg

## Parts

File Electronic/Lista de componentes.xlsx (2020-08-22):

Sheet: PLACA A1
Componentes placa A1
Cantidad | Nombre | Link | Descripción | Lugar de venta
1 | 53261-7006 | t.ly/xoT1 | Picoblade 6 pines, angulo recto | Mouser
1 | 53261-0871 | t.ly/t022 | Picoblade 8 pines, angulo recto | Mouser
1 | 53261-1271 | t.ly/Dxhb | Picoblade 12 pines, angulo recto | Mouser
1 | PMV16XNR | t.ly/uZRf | Mosfet | Mouser
2 | MCP9808T-E/MS | t.ly/6n5W | Sensor de temperatura (i2c) | Digikey
1 | ABM3-16.000MHZ-D2Y-T | t.ly/1RZ4 | Clock 16 MHz | Digikey
1 | - | - | Switch de reset arduino | -
4 | M1.6 X 5mm Torx Pan Head Screws (ISO 14583) - A2 Stainless Steel | t.ly/bRiH | Tornillos centrales | ACCU
6 | M1.6 Hexagon Nuts (DIN 934) - A2 Stainless Steel | t.ly/lHjF | Tuercas centrales | ACCU
8 | M1.6 Reduced Diameter Flat Washers (DIN 433) - A2 Stainless Steel | t.ly/oWgw | Golillas centrales | ACCU
2 | ERA-8AEB331V | t.ly/mJBy | Resistencia 330 Ohm (Switch) | Digikey
2 | ERA-8AEB472V | t.ly/z2e3 | Resistencia 4.7 kOhm (Pull up) | Digikey
1 | ERA-8AEB103V | t.ly/Jadm | Resistencia 10 kOhm (Mosfet) | Digikey
1 | C0402C104Z4VAC7867 | t.ly/kweN | Condensador 0.1 uF | Digikey
2 | C0603C104J4RACTU | t.ly/rFsq | Condensador 22 pF | Digikey
1 | AV4524 | t.ly/CNFJ | Switch (despliegue paneles) | Digikey
1 | D3SH-A1R1 | t.ly/lGXs | Switch (despliegue paneles) | Digikey

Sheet: PLACA B1
Componentes placa B1
Cantidad | Nombre | Link | Descripción | Lugar de venta
2 | 53261-0871 | t.ly/t022 | Picoblade 8 pines, angulo recto | Mouser
1 | PMV16XNR | t.ly/uZRf | Mosfet | Mouser
2 | MCP9808T-E/MS | t.ly/6n5W | Sensor de temperatura (i2c) | Digikey
4 | M1.6 X 8mm Torx Pan Head Screws (ISO 14583) - A2 Stainless Steel | t.ly/vgg6 | Tornillos centrales/soportes | ACCU
6 | M1.6 Hexagon Nuts (DIN 934) - A2 Stainless Steel | t.ly/lHjF | Tuercas centrales/soportes | ACCU
8 | M1.6 Reduced Diameter Flat Washers (DIN 433) - A2 Stainless Steel | t.ly/oWgw | Golillas centrales/soportes | ACCU
2 | ERA-8AEB331V | t.ly/mJBy | Resistencia 330 Ohm (Switch) | Digikey
1 | ERA-8AEB103V | t.ly/Jadm | Resistencia 10 kOhm (Mosfet) | Digikey
1 | AV4524 | t.ly/CNFJ | Switch (despliegue paneles) | Digikey
1 | D3SH-A1R1 | t.ly/lGXs | Switch (despliegue paneles) | Digikey

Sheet: PLACA A2
Componentes placa A2
Cantidad | Nombre | Link | Descripción | Lugar de venta
2 | 53261-7006 | t.ly/xoT1 | Picoblade 6 pines, angulo recto | Mouser
 | 53261-0871 | t.ly/t022 | Picoblade 8 pines, angulo recto | Mouser
1 | PMV16XNR | t.ly/uZRf | Mosfet | Mouser
2 | MCP9808T-E/MS | t.ly/6n5W | Sensor de temperatura (i2c) | Digikey
4 | M1.6 X 5mm Torx Pan Head Screws (ISO 14583) - A2 Stainless Steel | t.ly/bRiH | Tornillos centrales/soportes | ACCU
6 | M1.6 Hexagon Nuts (DIN 934) - A2 Stainless Steel | t.ly/lHjF | Tuercas centrales/soportes | ACCU
8 | M1.6 Reduced Diameter Flat Washers (DIN 433) - A2 Stainless Steel | t.ly/oWgw | Golillas centrales/soportes | ACCU
2 | ERA-8AEB331V | t.ly/mJBy | Resistencia 330 Ohm (Switch) | Digikey
1 | ERA-8AEB103V | t.ly/Jadm | Resistencia 10 kOhm (Mosfet) | Digikey
1 | AV4524 | t.ly/CNFJ | Switch (despliegue paneles) | Digikey
1 | D3SH-A1R1 | t.ly/lGXs | Switch (despliegue paneles) | Digikey

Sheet: PLACA B2
Componentes placa B2
Cantidad | Nombre | Link | Descripción | Lugar de venta
1 | 53261-7006 | t.ly/xoT1 | Picoblade 6 pines, angulo recto | Mouser
1 | 53261-7002 | t.ly/KGWQ | Picoblade 2 pines, angulo recto | Mouser
1 | PMV16XNR | t.ly/uZRf | Mosfet | Mouser
2 | MCP9808T-E/MS | t.ly/6n5W | Sensor de temperatura (i2c) | Digikey
3 | M1.6 X 5mm Torx Pan Head Screws (ISO 14583) - A2 Stainless Steel | t.ly/bRiH | Tornillos centrales | ACCU
5 | M1.6 Hexagon Nuts (DIN 934) - A2 Stainless Steel | t.ly/lHjF | Tuercas centrales | ACCU
6 | M1.6 Reduced Diameter Flat Washers (DIN 433) - A2 Stainless Steel | t.ly/oWgw | Golillas centrales | ACCU
2 | ERA-8AEB331V | t.ly/mJBy | Resistencia 330 Ohm (Switch) | Digikey
1 | ERA-8AEB103V | t.ly/Jadm | Resistencia 10 kOhm (Mosfet) | Digikey
1 | AV4524 | t.ly/CNFJ | Switch (despliegue paneles) | Digikey
1 | D3SH-A1R1 | t.ly/lGXs | Switch (despliegue paneles) SMD | Digikey

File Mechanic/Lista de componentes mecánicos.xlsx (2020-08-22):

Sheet: PLACA A1
Componentes placa A1
Cantidad | Nombre | Link | Descripción | Lugar de venta
4 | M1.6 X 8mm Torx Pan Head Screws (ISO 14583) - A2 Stainless Steel | t.ly/HROZ | Tornillos centrales/soportes | ACCU
6 | M1.6 Hexagon Nuts (DIN 934) - A2 Stainless Steel | t.ly/lHjF | Tuercas centrales/soportes | ACCU
8 | M1.6 Reduced Diameter Flat Washers (DIN 433) - A2 Stainless Steel | t.ly/oWgw | Golillas centrales/soportes | ACCU

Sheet: PLACA B1
Componentes placa B1
Cantidad | Nombre | Link | Descripción | Lugar de venta
4 | M1.6 X 8mm Torx Pan Head Screws (ISO 14583) - A2 Stainless Steel | t.ly/HROZ | Tornillos centrales/soportes | ACCU
6 | M1.6 Hexagon Nuts (DIN 934) - A2 Stainless Steel | t.ly/lHjF | Tuercas centrales/soportes | ACCU
8 | M1.6 Reduced Diameter Flat Washers (DIN 433) - A2 Stainless Steel | t.ly/oWgw | Golillas centrales/soportes | ACCU

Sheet: PLACA A2
Componentes placa A2
Cantidad | Nombre | Link | Descripción | Lugar de venta
4 | M1.6 X 5mm Torx Pan Head Screws (ISO 14583) - A2 Stainless Steel | t.ly/HROZ | Tornillos centrales/soportes | ACCU
6 | M1.6 Hexagon Nuts (DIN 934) - A2 Stainless Steel | t.ly/lHjF | Tuercas centrales/soportes | ACCU
8 | M1.6 Reduced Diameter Flat Washers (DIN 433) - A2 Stainless Steel | t.ly/oWgw | Golillas centrales/soportes | ACCU

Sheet: PLACA B2
Componentes placa B2
Cantidad | Nombre | Link | Descripción | Lugar de venta
4 | M1.6 X 8mm Torx Pan Head Screws (ISO 14583) - A2 Stainless Steel | t.ly/HROZ | Tornillos centrales/soportes | ACCU
6 | M1.6 Hexagon Nuts (DIN 934) - A2 Stainless Steel | t.ly/lHjF | Tuercas centrales/soportes | ACCU
8 | M1.6 Reduced Diameter Flat Washers (DIN 433) - A2 Stainless Steel | t.ly/oWgw | Golillas centrales/soportes | ACCU

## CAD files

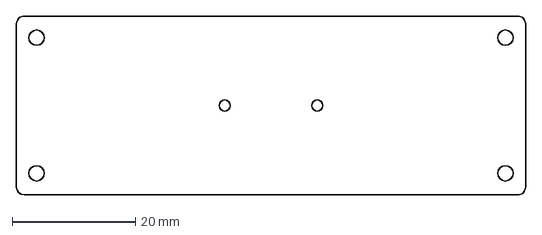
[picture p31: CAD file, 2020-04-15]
Mechanic/DXF files (originales)/interstageV2-AOutLine_intgssbA-2(Low).dxf
82.5 x 29.0 mm

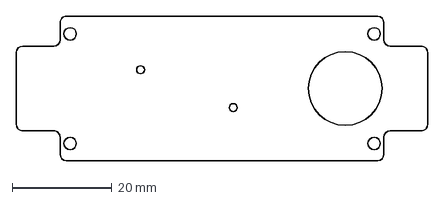
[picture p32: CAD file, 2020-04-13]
Mechanic/DXF files/HoldVersionIS.dxf
82.5 x 29.0 mm

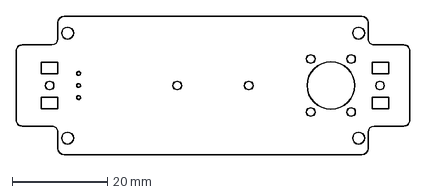
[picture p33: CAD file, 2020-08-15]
Mechanic/DXF placas/DXF/Placa B2.dxf
82.5 x 29.0 mm

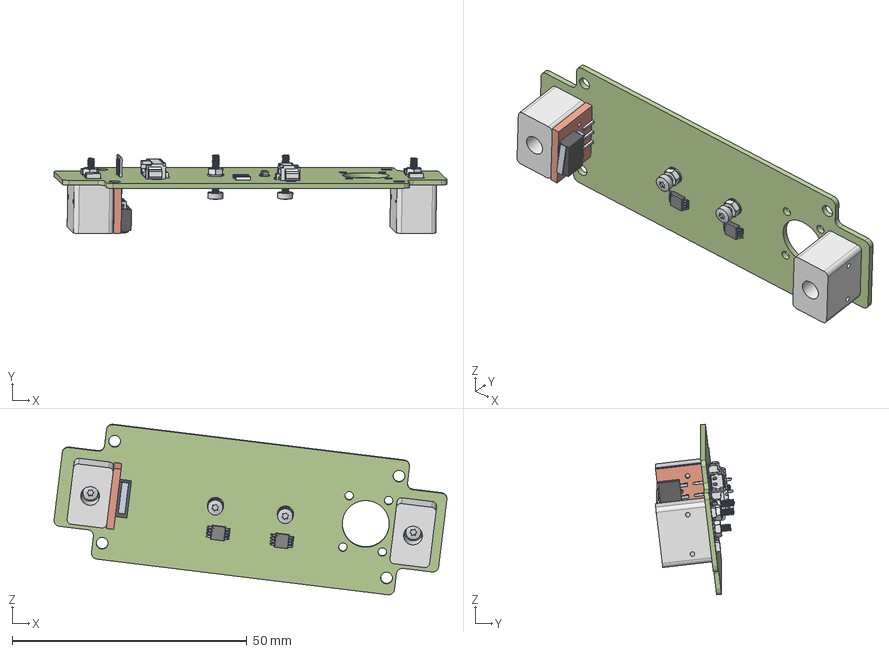
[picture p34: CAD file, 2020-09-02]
Mechanic/Piezas/Placas/Placa B2 v2_tht.stp
83.7 x 16.8 x 36.3 mm
Interstage B2
Mosfet PMV16XNR
Golilla M1.6 x 8
Tuerca M1.6_2 x 6
Soporte placa 2.0 x 2
Tornillo M1.6 8 mm x 4
Picoblade 2
Picoblade 6
Resistencia 330 Ohm ERA-8APB1581V- x 2
Sensor MCP9808T x 2
Placa Cobre
Switch AV4524_1
Conector 3 pines

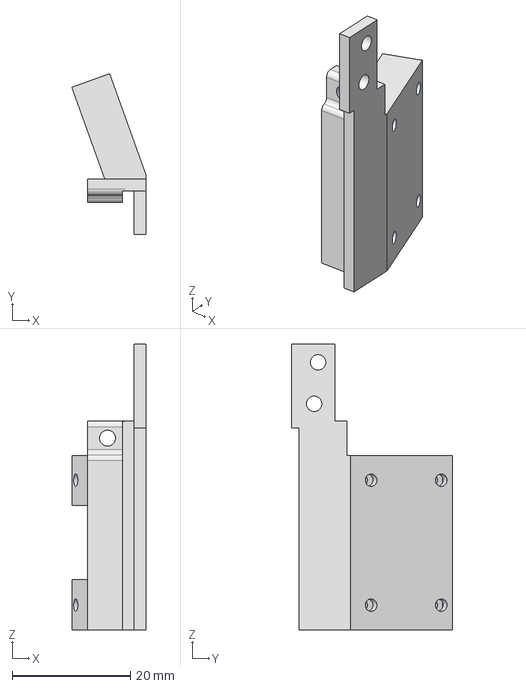
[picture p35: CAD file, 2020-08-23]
Mechanic/Piezas/Soporte Cámara.stp
12.6 x 27.1 x 48.3 mm

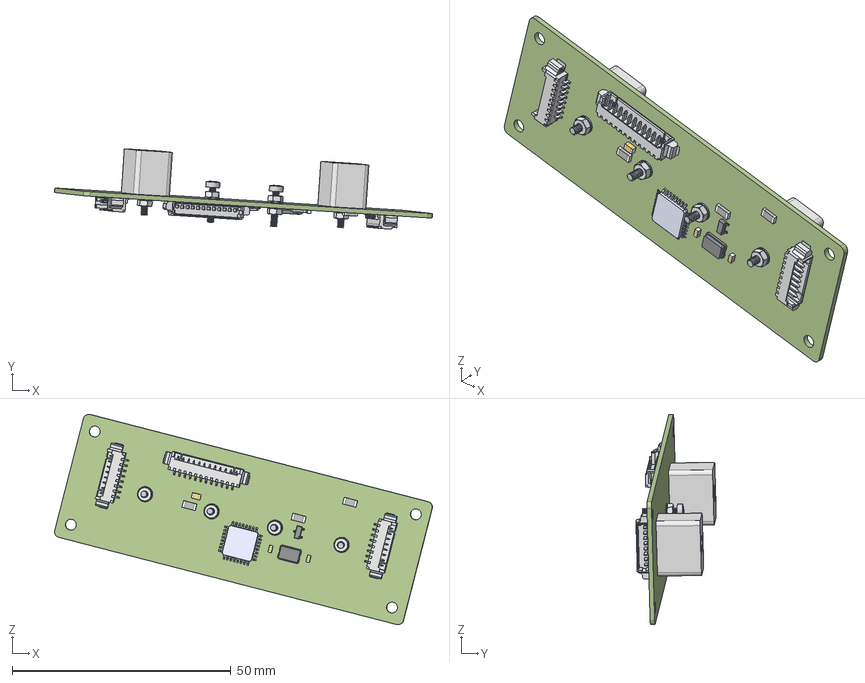
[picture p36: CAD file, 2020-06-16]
Mechanic/Soporte v2/Placa A1 v2.stp
86.4 x 18.4 x 48.1 mm
Interstage A
R1206
Resistencia 330 Ohm x 2
Condensador 100nF
Condensador 22pF x 2
Mosfet PMV16XNR
ATMEGA328P
Golilla M1.6 x 8
Picoblade 8 x 2
Picoblade_2
Clock ABM3-16.000MHZ-D2Y-T
Soporte placa 2.0 x 2
Tornillo M1.6 8 mm x 4
Tuerca M1.6_2 x 6

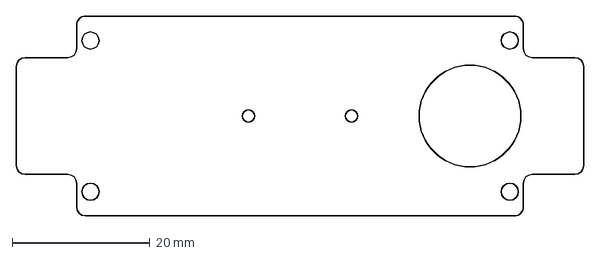
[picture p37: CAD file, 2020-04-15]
Mechanic/DXF files (originales)/HoleVersionIS.dxf
82.5 x 29.0 mm

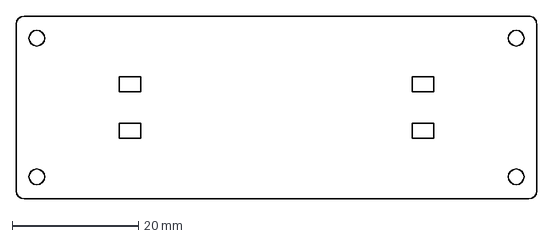
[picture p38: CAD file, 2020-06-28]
Mechanic/DXF placas/DXF/Placa A.dxf
82.5 x 29.0 mm

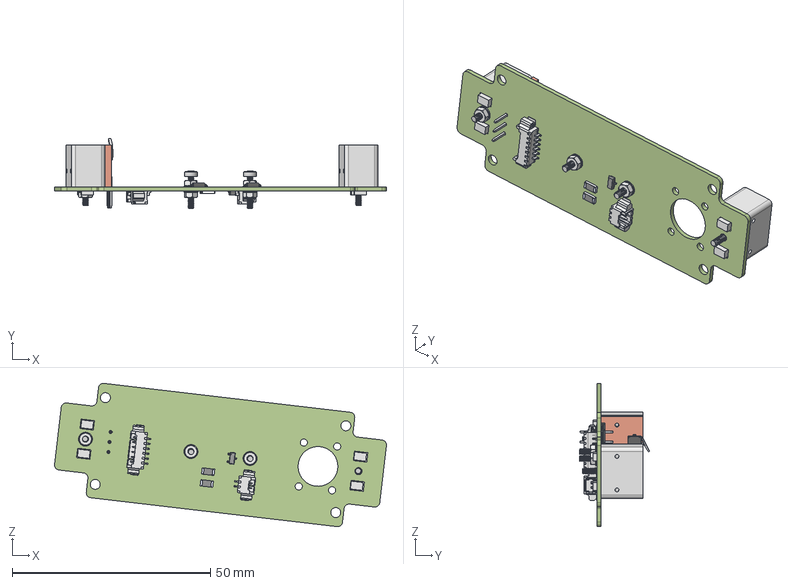
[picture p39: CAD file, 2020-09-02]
Mechanic/Piezas/Placas/Placa B2 v2_smd.stp
83.6 x 17.6 x 36.1 mm
Interstage B2
Mosfet PMV16XNR
Golilla M1.6 x 7
Tuerca M1.6_2 x 5
Soporte placa 2.0 x 2
Tornillo M1.6 8 mm x 4
Picoblade 2
Picoblade 6
Resistencia 330 Ohm ERA-8APB1581V- x 2
Sensor MCP9808T x 2
Placa Cobre
Switch D3SH-A1R1_1
Conector 3 pines

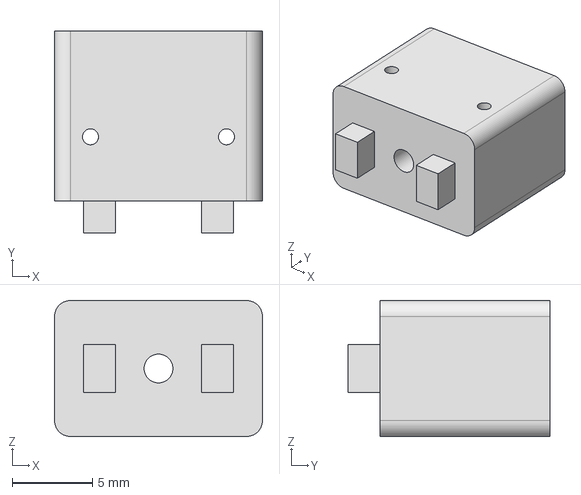
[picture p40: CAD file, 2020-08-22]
Mechanic/Piezas/Soporte Paneles.stp
13.0 x 12.6 x 8.50 mm

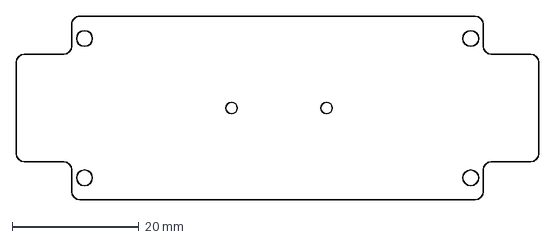
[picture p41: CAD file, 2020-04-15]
Mechanic/DXF files (originales)/interstageV2-BOutLine_intgssbB-2(Low).dxf
82.5 x 29.0 mm

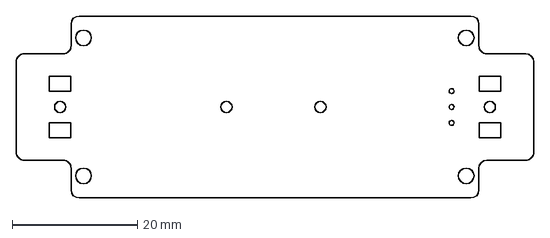
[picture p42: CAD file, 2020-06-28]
Mechanic/DXF placas/DXF/Placa B1.dxf
82.5 x 29.0 mm

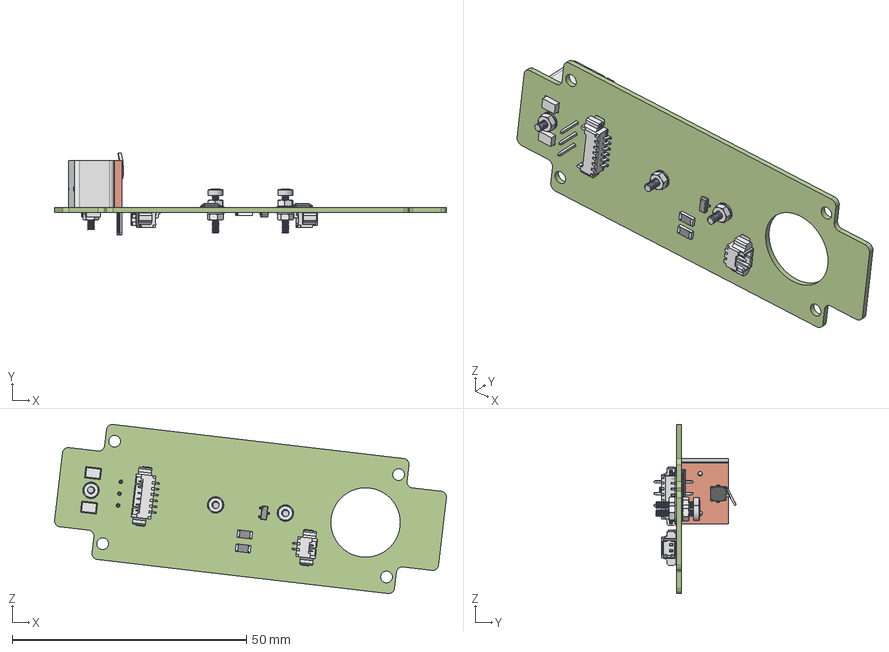
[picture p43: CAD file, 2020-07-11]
Mechanic/Piezas/Placas/Placa B2 smd.stp
83.6 x 17.4 x 36.1 mm
Interstage B2
Mosfet PMV16XNR
Golilla M1.6 x 6
Tuerca M1.6_2 x 5
Soporte placa 2.0
Tornillo M1.6 8 mm x 3
Picoblade 2
Picoblade 6
Resistencia 330 Ohm ERA-8APB1581V- x 2
Sensor MCP9808T x 2
Placa Cobre
Switch D3SH-A1R1_1
Conector 3 pines

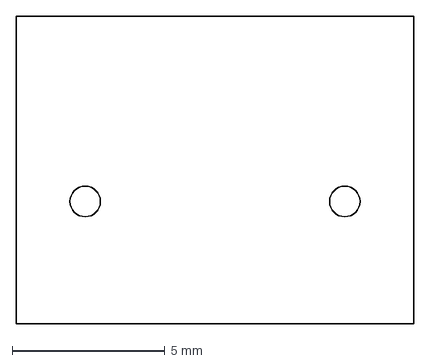
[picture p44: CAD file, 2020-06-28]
Mechanic/DXF placas/DXF/Placa Cobre.dxf
13.0 x 10.1 mm

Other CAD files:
Mechanic/Piezas/Placas/Placa B1 smd.stp
Mechanic/Piezas/Placas/Placa B2 tht.stp
Mechanic/Piezas/Placas/Placa B1 tht.stp
Mechanic/Piezas/Placas/Placa A2 smd.stp
Mechanic/Piezas/Placas/Placa A2 tht.stp

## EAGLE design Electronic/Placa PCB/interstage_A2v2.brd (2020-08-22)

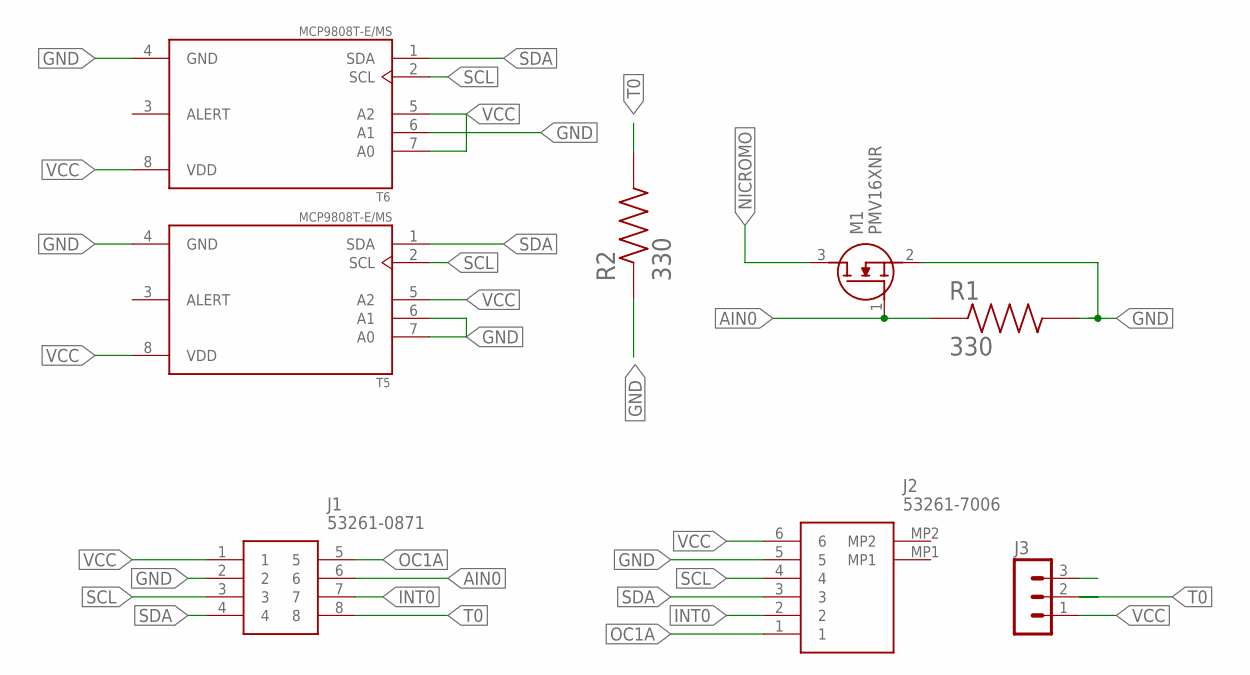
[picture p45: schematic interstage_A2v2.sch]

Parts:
J1: 53261-0871
J2: 53261-7006; 532617006
J3: MA03-1
M1: PMV16XNR; SOT95P230X110-3N
R1, R2: 330; RESC3216X70N
T5, T6: MCP9808T-E/MS; SOP65P490X110-8N

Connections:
AIN0: J1.6, M1.1 (G), R1.1
GND: J1.2, J2.5, M1.2 (S), R1.2, R2.1, T5.4 (GND), T5.6 (A1), T5.7 (A0), T6.4 (GND), T6.6 (A1)
INT0: J1.7, J2.2
NICROMO: M1.3 (D)
OC1A: J1.5, J2.1
SCL: J1.3, J2.4, T5.2 (SCL), T6.2 (SCL)
SDA: J1.4, J2.3, T5.1 (SDA), T6.1 (SDA)
T0: J1.8, J3.2, R2.2
VCC: J1.1, J2.6, J3.1, T5.5 (A2), T5.8 (VDD), T6.5 (A2), T6.7 (A0), T6.8 (VDD)

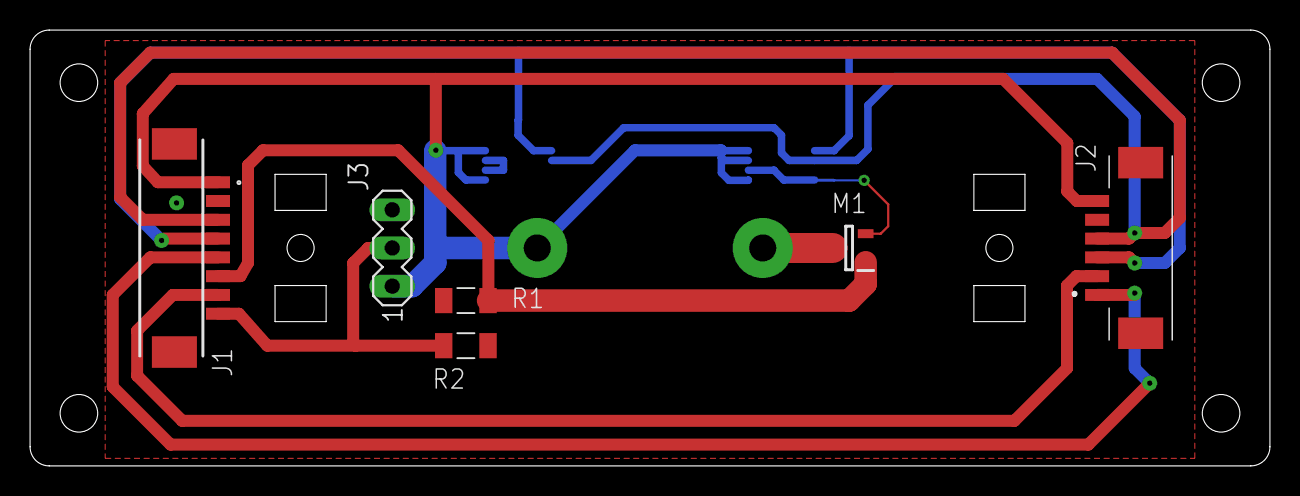
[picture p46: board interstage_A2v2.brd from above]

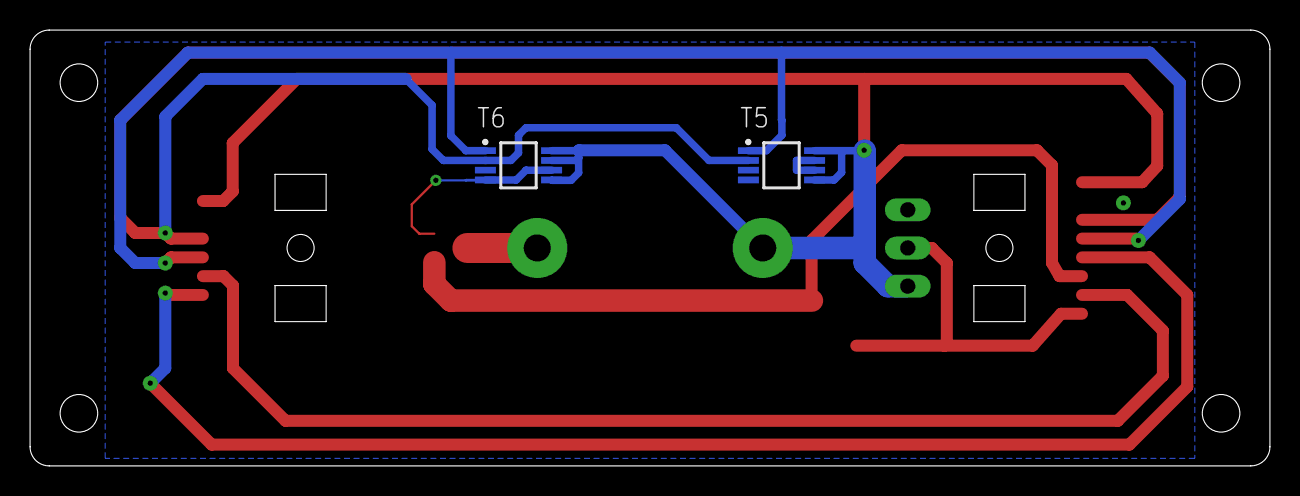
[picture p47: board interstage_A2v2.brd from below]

Board: 2 copper layers, 82.5 x 29.0 mm, 8 parts (2 on the bottom side), 8 nets.

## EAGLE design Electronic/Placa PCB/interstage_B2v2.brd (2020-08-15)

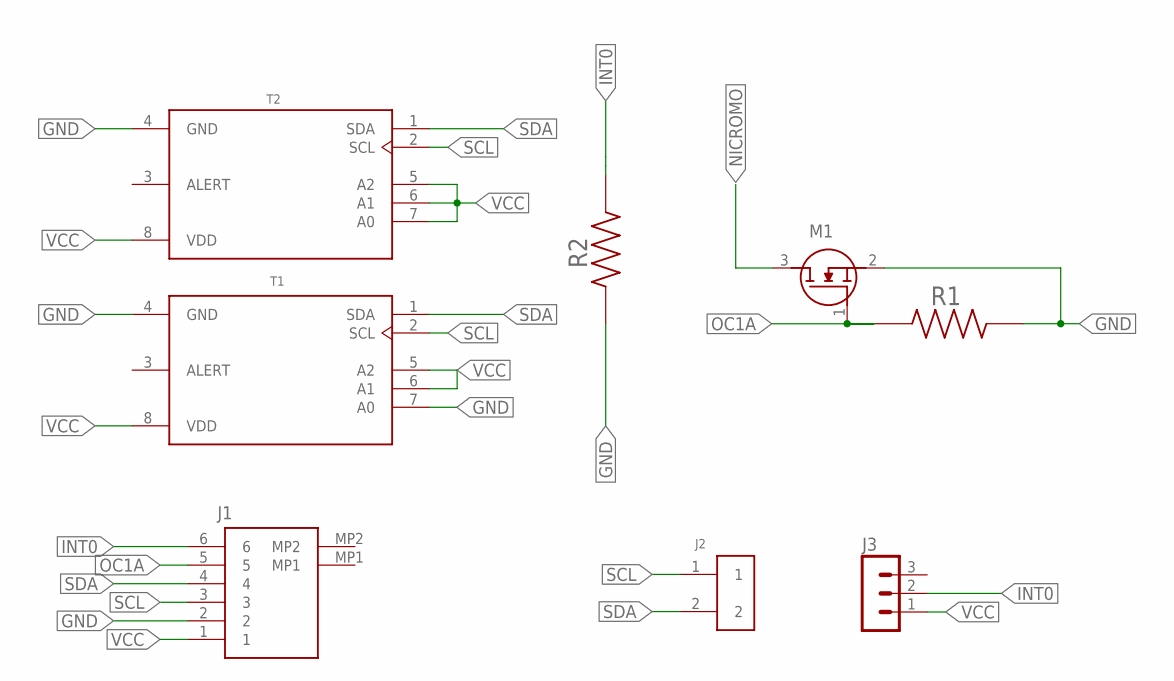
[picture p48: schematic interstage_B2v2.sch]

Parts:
J1: 53261-7006; 532617006
J2: 0532610271; MOLEX_0532610271
J3: MA03-1
M1: PMV16XNR; SOT95P230X110-3N
R1, R2: 330; RESC3216X70N
T1, T2: MCP9808T-E/MS; SOP65P490X110-8N

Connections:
GND: J1.2, M1.2 (S), R1.2, R2.1, T1.4 (GND), T1.7 (A0), T2.4 (GND)
INT0: J1.6, J3.2, R2.2
NICROMO: M1.3 (D)
OC1A: J1.5, M1.1 (G), R1.1
SCL: J1.3, J2.1, T1.2 (SCL), T2.2 (SCL)
SDA: J1.4, J2.2, T1.1 (SDA), T2.1 (SDA)
VCC: J1.1, J3.1, T1.5 (A2), T1.6 (A1), T1.8 (VDD), T2.5 (A2), T2.6 (A1), T2.7 (A0), T2.8 (VDD)

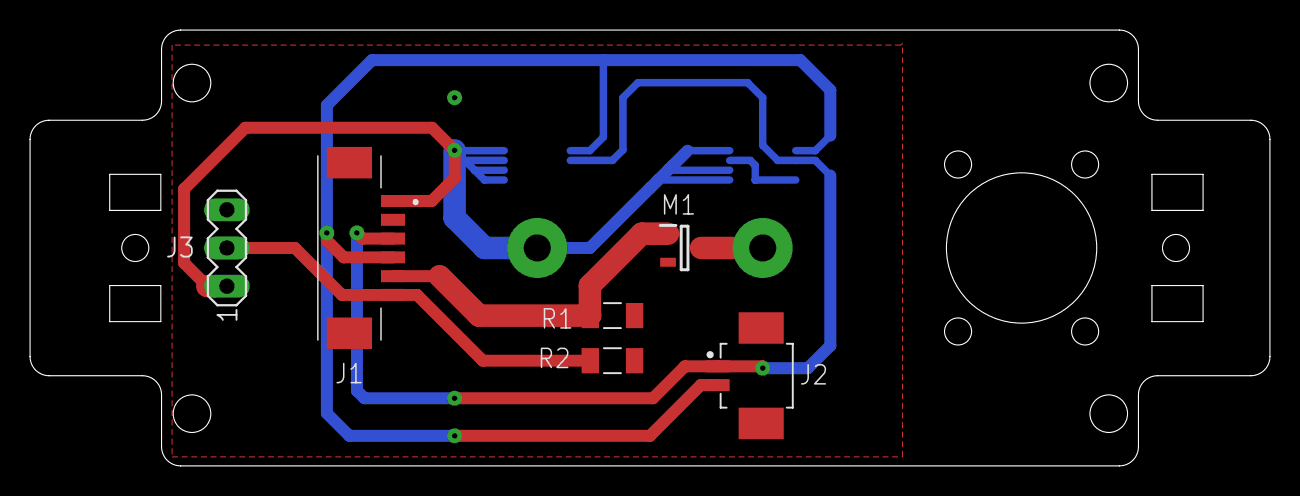
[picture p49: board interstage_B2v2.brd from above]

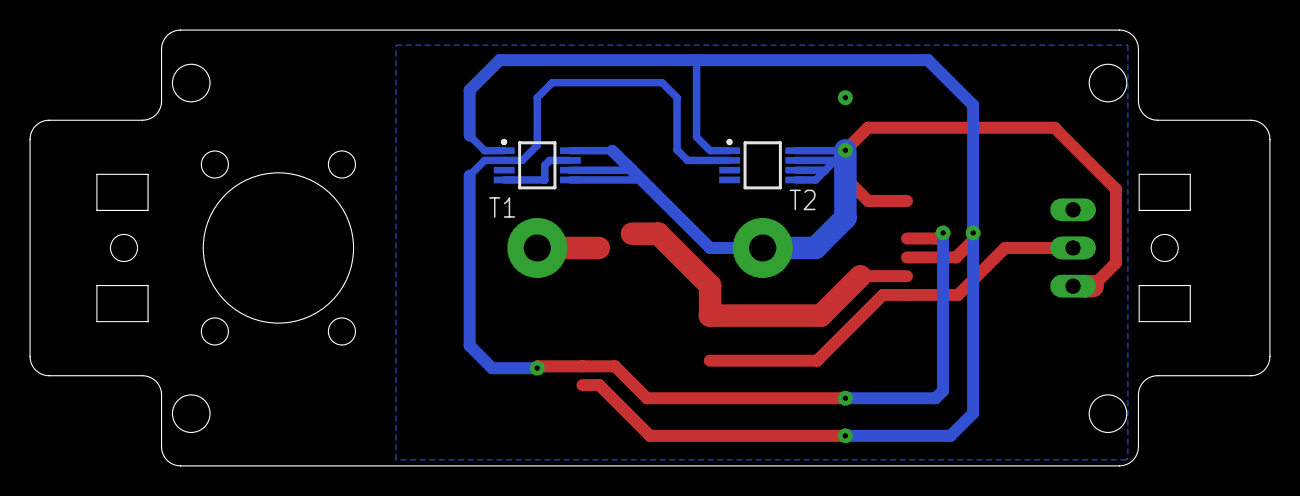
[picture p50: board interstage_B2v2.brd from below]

Board: 2 copper layers, 82.5 x 29.0 mm, 8 parts (2 on the bottom side), 6 nets.

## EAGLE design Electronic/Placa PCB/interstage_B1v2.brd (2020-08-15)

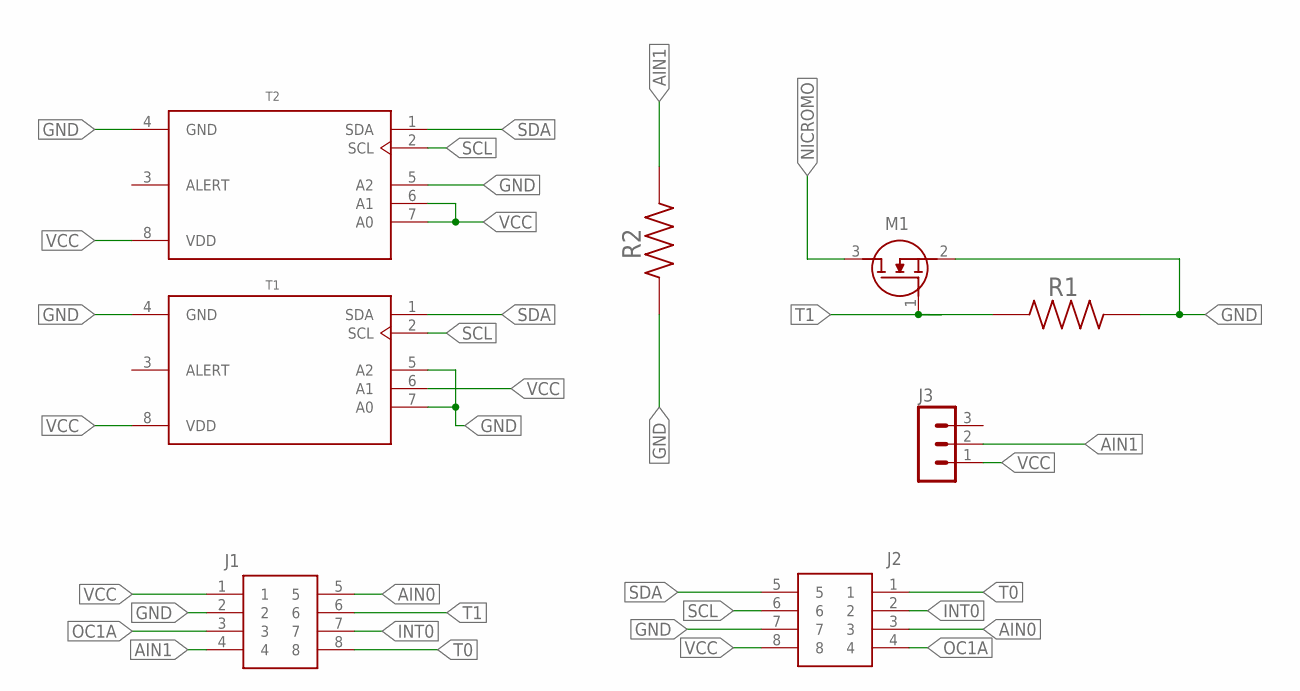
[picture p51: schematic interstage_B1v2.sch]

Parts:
J1, J2: 53261-0871
J3: MA03-1
M1: PMV16XNR; SOT95P230X110-3N
R1, R2: 330; RESC3216X70N
T1, T2: MCP9808T-E/MS; SOP65P490X110-8N

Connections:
AIN0: J1.5, J2.3
AIN1: J1.4, J3.2, R2.2
GND: J1.2, J2.7, M1.2 (S), R1.2, R2.1, T1.4 (GND), T1.5 (A2), T1.7 (A0), T2.4 (GND), T2.5 (A2)
INT0: J1.7, J2.2
NICROMO: M1.3 (D)
OC1A: J1.3, J2.4
SCL: J2.6, T1.2 (SCL), T2.2 (SCL)
SDA: J2.5, T1.1 (SDA), T2.1 (SDA)
T0: J1.8, J2.1
T1: J1.6, M1.1 (G), R1.1
VCC: J1.1, J2.8, J3.1, T1.6 (A1), T1.8 (VDD), T2.6 (A1), T2.7 (A0), T2.8 (VDD)

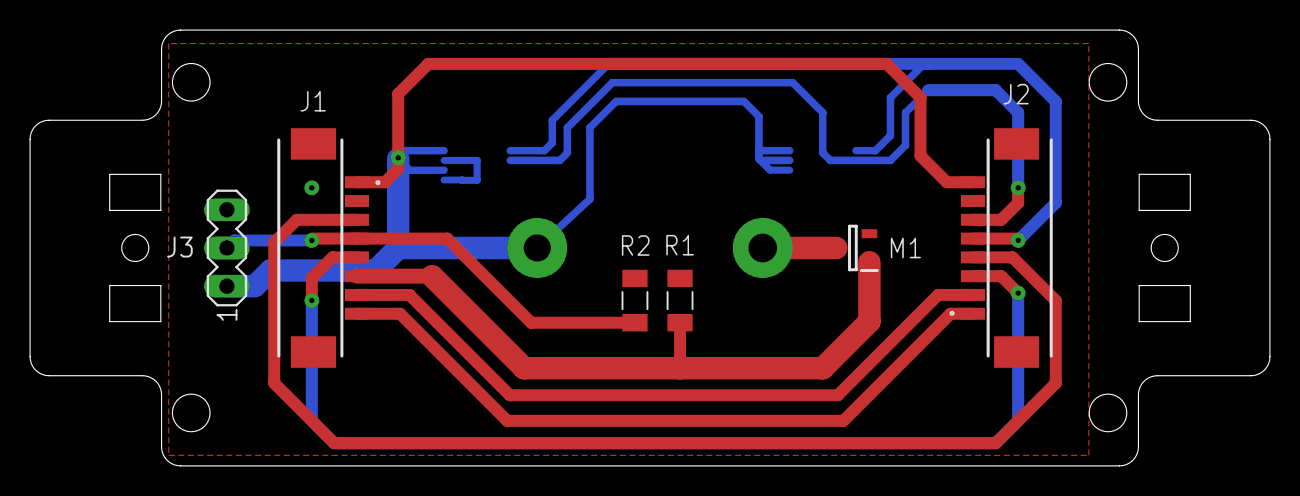
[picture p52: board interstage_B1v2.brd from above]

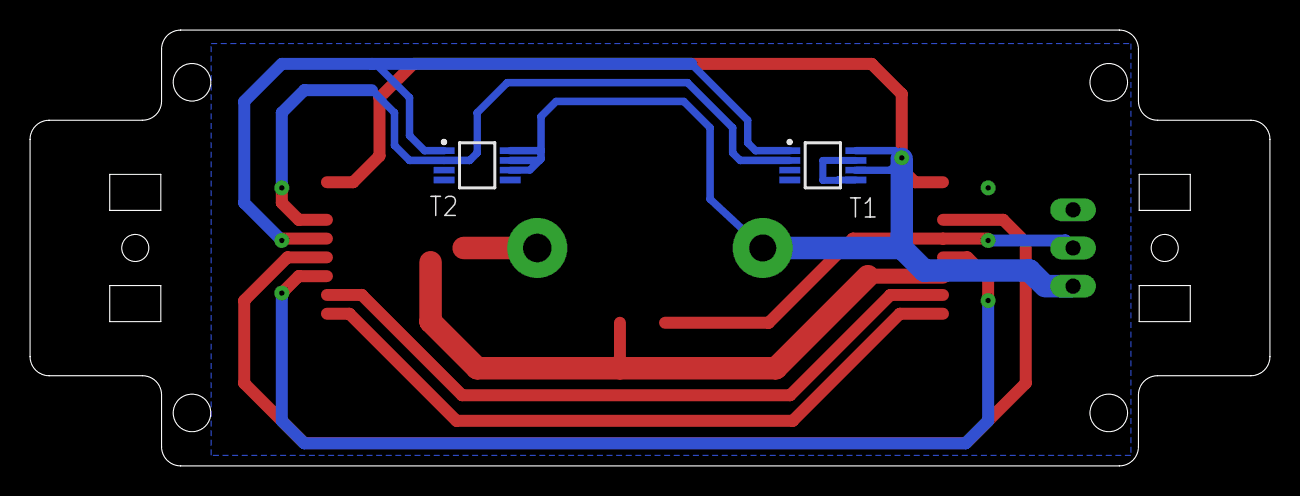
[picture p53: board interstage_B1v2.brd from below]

Board: 2 copper layers, 82.5 x 29.0 mm, 8 parts (2 on the bottom side), 10 nets.

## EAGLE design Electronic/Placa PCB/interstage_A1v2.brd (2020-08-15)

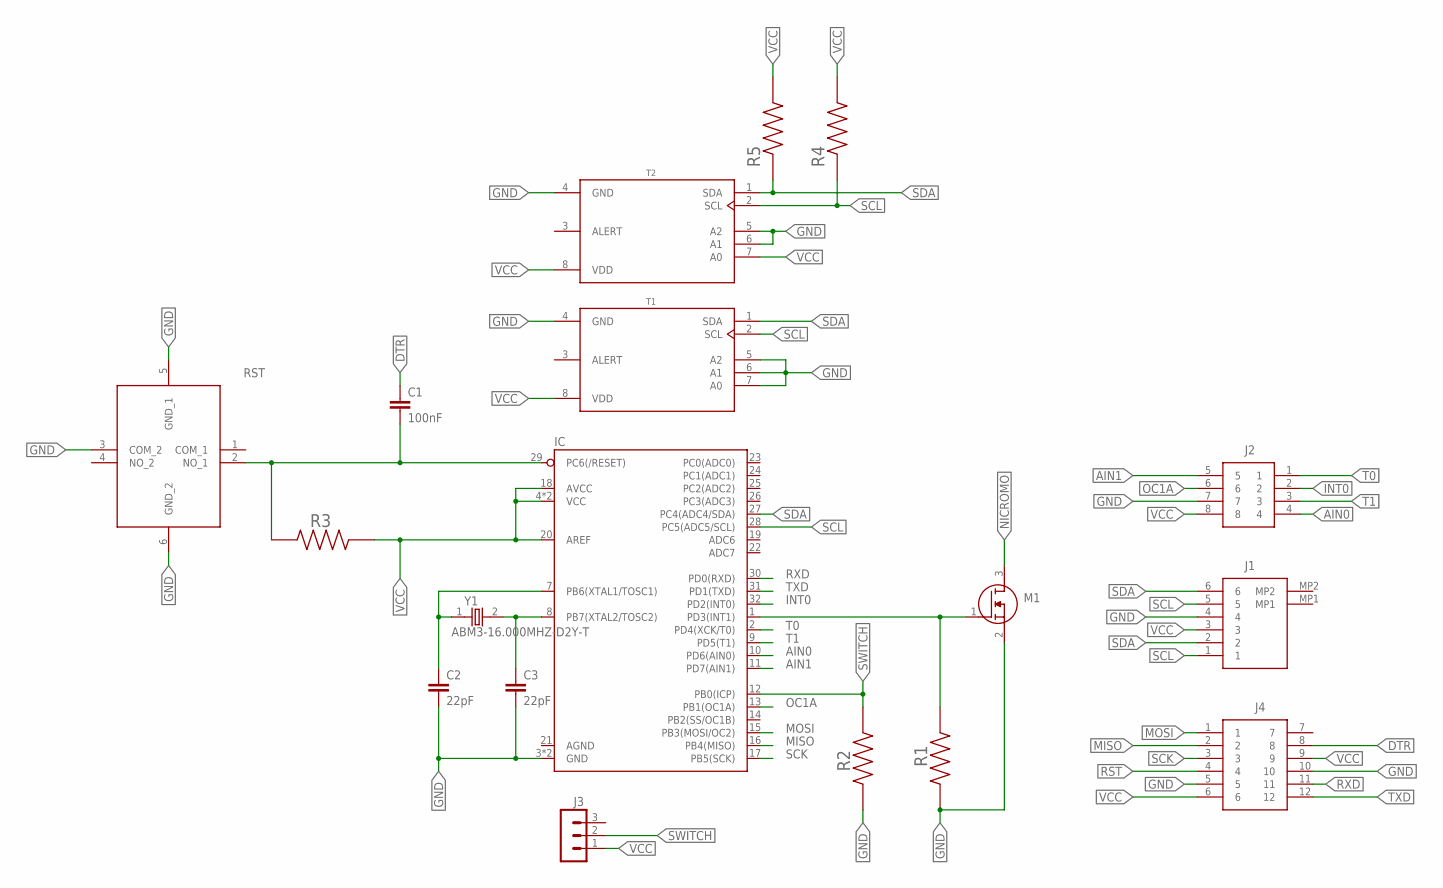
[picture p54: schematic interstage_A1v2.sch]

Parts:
C1: 100nF; C0805K
C2, C3: 22pF; C0603K
IC: ATMEGA328P_TQFP; TQFP32-08
J1: 53261-7006; 532617006
J2: 53261-0871
J3: MA03-1
J4: 53261-1271
M1: PMV16XNR; SOT95P230X110-3N
R1, R2: 330; RESC3216X70N
R3: 10k; RESC3216X70N
R4, R5: 4.7k; RESC3216X70N
RST: 431151015826
T1, T2: MCP9808T-E/MS; SOP65P490X110-8N
Y1: ABM3-16.000MHZ-D2Y-T; XTAL500X320X130N

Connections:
AIN0: IC.10 (PD6(AIN0)), J2.4
AIN1: IC.11 (PD7(AIN1)), J2.5
DTR: C1.1, J4.8
GND: C2.2, C3.2, IC.3 (GND), IC.5 (GND), J1.4, J2.7, J4.5, J4.10, M1.2 (S), R1.2, R2.1, RST.3 (COM_2), RST.5 (GND_1), RST.6 (GND_2), T1.4 (GND), T1.5 (A2), T1.6 (A1), T1.7 (A0), T2.4 (GND), T2.5 (A2), T2.6 (A1)
INT0: IC.32 (PD2(INT0)), J2.2
INT1: IC.1 (PD3(INT1)), M1.1 (G), R1.1
MISO: IC.16 (PB4(MISO)), J4.2
MOSI: IC.15 (PB3(MOSI/OC2)), J4.1
unnamed: C2.1, IC.7 (PB6(XTAL1/TOSC1)), Y1.1
unnamed: C3.1, IC.8 (PB7(XTAL2/TOSC2)), Y1.2
NICROMO: M1.3 (D)
OC1A: IC.13 (PB1(OC1A)), J2.6
RST: C1.2, IC.29 (PC6(/RESET)), J4.4, R3.1, RST.2 (NO_1)
RXD: IC.30 (PD0(RXD)), J4.11
SCK: IC.17 (PB5(SCK)), J4.3
SCL: IC.28 (PC5(ADC5/SCL)), J1.1, J1.5, R4.1, T1.2 (SCL), T2.2 (SCL)
SDA: IC.27 (PC4(ADC4/SDA)), J1.2, J1.6, R5.1, T1.1 (SDA), T2.1 (SDA)
SWITCH: IC.12 (PB0(ICP)), J3.2, R2.2
T0: IC.2 (PD4(XCK/T0)), J2.1
T1: IC.9 (PD5(T1)), J2.3
TXD: IC.31 (PD1(TXD)), J4.12
VCC: IC.4 (VCC), IC.6 (VCC), IC.18 (AVCC), IC.20 (AREF), J1.3, J2.8, J3.1, J4.6, J4.9, R3.2, R4.2, R5.2, T1.8 (VDD), T2.7 (A0), T2.8 (VDD)

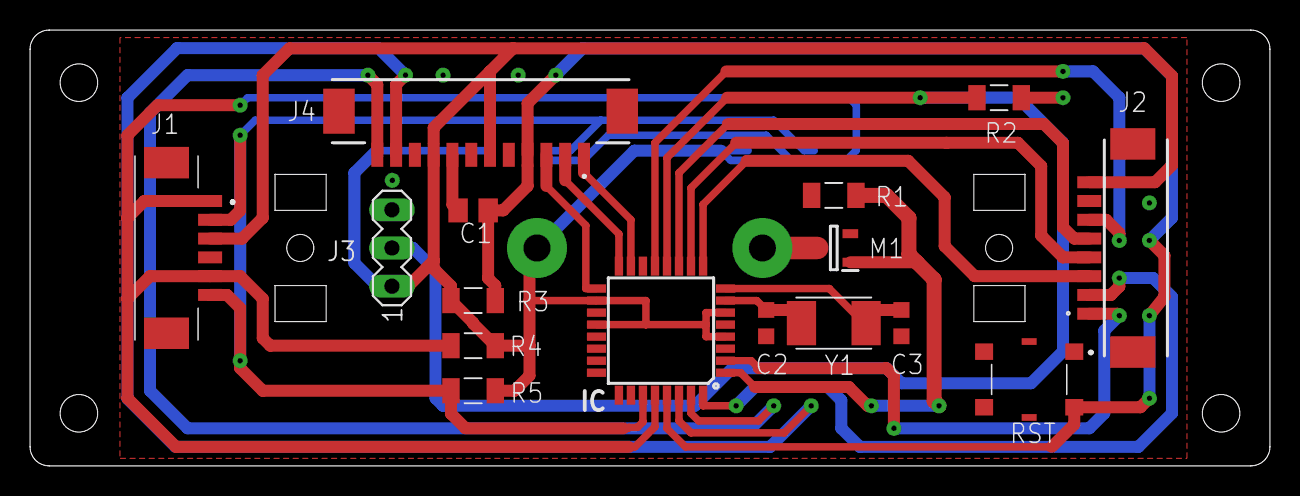
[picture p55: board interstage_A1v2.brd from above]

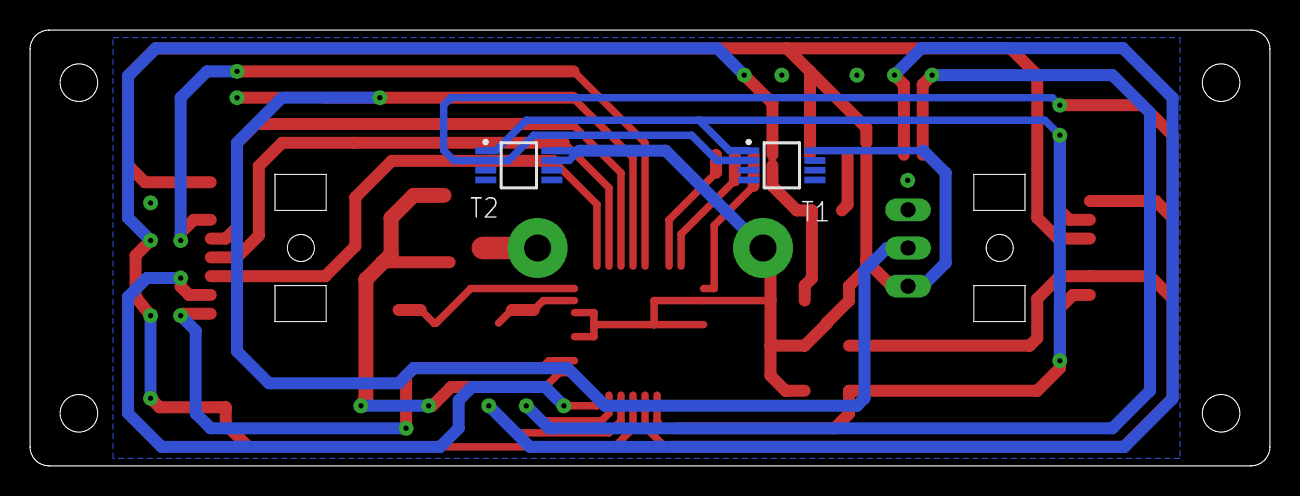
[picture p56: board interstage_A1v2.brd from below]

Board: 2 copper layers, 82.5 x 29.0 mm, 18 parts (2 on the bottom side), 21 nets.

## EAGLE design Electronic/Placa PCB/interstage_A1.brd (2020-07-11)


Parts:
B2/OBC: 53261-7006; 532617006
BOOTLOADER/FTDI: 53261-1271
C1: 100nF; C0805K
C4, C5: 22pF; C0603K
CONEXION_B1: 53261-0871
J1: 431151015826
PINES_SWITCH: MA03-1
Q1: PMV16XNR; SOT95P230X110-3N
R_MOS: ERA-8AEB331V; RESC3216X70N
R_PULL1, R_PULL2: ERA-8AEB472V; RESC3216X70N
R_RST: ERA-8AEB103V; RESC3216X70N
R_SWITCH: ERA-8AEB331V; RESC3216X70N
T1, T2: MCP9808T-E/MS; SOP65P490X110-8N
U2: ATMEGA328P_TQFP; TQFP32-08
Y2: ABM3-16.000MHZ-D2Y-T; XTAL500X320X130N

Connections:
AIN0: CONEXION_B1.4, U2.10 (PD6(AIN0))
AIN1: CONEXION_B1.5, U2.11 (PD7(AIN1))
DTR: BOOTLOADER/FTDI.8, C1.1
GND: B2/OBC.4, BOOTLOADER/FTDI.5, BOOTLOADER/FTDI.10, C4.2, C5.2, CONEXION_B1.7, J1.3 (COM_2), J1.5 (GND_1), J1.6 (GND_2), Q1.2 (S), R_MOS.2, R_SWITCH.1, T1.4 (GND), T1.5 (A2), T1.6 (A1), T1.7 (A0), T2.4 (GND), T2.5 (A2), T2.6 (A1), U2.3 (GND), U2.5 (GND)
INT0: CONEXION_B1.2, U2.32 (PD2(INT0))
INT1: Q1.1 (G), R_MOS.1, U2.1 (PD3(INT1))
MISO: BOOTLOADER/FTDI.2, U2.16 (PB4(MISO))
MOSI: BOOTLOADER/FTDI.1, U2.15 (PB3(MOSI/OC2))
unnamed: C5.1, U2.7 (PB6(XTAL1/TOSC1)), Y2.1
unnamed: C4.1, U2.8 (PB7(XTAL2/TOSC2)), Y2.2
NICROMO: Q1.3 (D)
OC1A: CONEXION_B1.6, U2.13 (PB1(OC1A))
RST: BOOTLOADER/FTDI.4, C1.2, J1.2 (NO_1), R_RST.1, U2.29 (PC6(/RESET))
RXD: BOOTLOADER/FTDI.11, U2.30 (PD0(RXD))
SCK: BOOTLOADER/FTDI.3, U2.17 (PB5(SCK))
SCL: B2/OBC.1, B2/OBC.5, R_PULL1.1, T1.2 (SCL), T2.2 (SCL), U2.28 (PC5(ADC5/SCL))
SDA: B2/OBC.2, B2/OBC.6, R_PULL2.1, T1.1 (SDA), T2.1 (SDA), U2.27 (PC4(ADC4/SDA))
SWITCH: PINES_SWITCH.2, R_SWITCH.2, U2.12 (PB0(ICP))
T0: CONEXION_B1.1, U2.2 (PD4(XCK/T0))
T1: CONEXION_B1.3, U2.9 (PD5(T1))
TXD: BOOTLOADER/FTDI.12, U2.31 (PD1(TXD))
VCC: B2/OBC.3, BOOTLOADER/FTDI.6, BOOTLOADER/FTDI.9, CONEXION_B1.8, PINES_SWITCH.1, R_PULL1.2, R_PULL2.2, R_RST.2, T1.8 (VDD), T2.7 (A0), T2.8 (VDD), U2.4 (VCC), U2.6 (VCC), U2.18 (AVCC), U2.20 (AREF)



Board: 2 copper layers, 82.5 x 29.0 mm, 18 parts (2 on the bottom side), 21 nets.

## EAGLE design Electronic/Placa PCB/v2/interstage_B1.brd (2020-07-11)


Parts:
CONEXION_A1, CONEXION_A2: 53261-0871
Q1: PMV16XNR; SOT95P230X110-3N
R_MOSFET: ERA-8AEB331V; RESC3216X70N
R_SWITCH: ERA-8AEB331V; RESC3216X70N
SV1: MA03-1
T3, T4: MCP9808T-E/MS; SOP65P490X110-8N

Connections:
AIN0: CONEXION_A1.5, CONEXION_A2.3
AIN1: CONEXION_A1.4, R_SWITCH.2, SV1.2
GND: CONEXION_A1.2, CONEXION_A2.7, Q1.2 (S), R_MOSFET.2, R_SWITCH.1, T3.4 (GND), T3.5 (A2), T3.7 (A0), T4.4 (GND), T4.5 (A2)
INT0: CONEXION_A1.7, CONEXION_A2.2
NICROMO: Q1.3 (D)
OC1A: CONEXION_A1.3, CONEXION_A2.4
SCL: CONEXION_A2.6, T3.2 (SCL), T4.2 (SCL)
SDA: CONEXION_A2.5, T3.1 (SDA), T4.1 (SDA)
T0: CONEXION_A1.8, CONEXION_A2.1
T1: CONEXION_A1.6, Q1.1 (G), R_MOSFET.1
VCC: CONEXION_A1.1, CONEXION_A2.8, SV1.1, T3.6 (A1), T3.8 (VDD), T4.6 (A1), T4.7 (A0), T4.8 (VDD)



Board: 2 copper layers, 82.5 x 29.0 mm, 8 parts (2 on the bottom side), 10 nets.

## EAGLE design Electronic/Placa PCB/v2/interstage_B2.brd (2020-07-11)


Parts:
CONEXION_A1: 0532610271; MOLEX_0532610271
CONEXION_A2: 53261-7006; 532617006
Q1: PMV16XNR; SOT95P230X110-3N
R_MOSFET: ERA-8AEB331V; RESC3216X70N
R_SWITCH: ERA-8AEB331V; RESC3216X70N
SV1: MA03-1
T7, T8: MCP9808T-E/MS; SOP65P490X110-8N

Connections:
GND: CONEXION_A2.2, Q1.2 (S), R_MOSFET.2, R_SWITCH.1, T7.4 (GND), T7.7 (A0), T8.4 (GND)
INT0: CONEXION_A2.6, R_SWITCH.2, SV1.2
NICROMO: Q1.3 (D)
OC1A: CONEXION_A2.5, Q1.1 (G), R_MOSFET.1
SCL: CONEXION_A1.1, CONEXION_A2.3, T7.2 (SCL), T8.2 (SCL)
SDA: CONEXION_A1.2, CONEXION_A2.4, T7.1 (SDA), T8.1 (SDA)
VCC: CONEXION_A2.1, SV1.1, T7.5 (A2), T7.6 (A1), T7.8 (VDD), T8.5 (A2), T8.6 (A1), T8.7 (A0), T8.8 (VDD)

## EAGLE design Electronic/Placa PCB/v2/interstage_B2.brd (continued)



Board: 2 copper layers, 82.5 x 29.0 mm, 8 parts (2 on the bottom side), 6 nets.

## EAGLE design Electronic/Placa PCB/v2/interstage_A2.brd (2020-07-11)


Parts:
CONEXION_B1: 53261-0871
CONEXION_B2: 53261-7006; 532617006
PINES_SWITCH: MA03-1
Q1: PMV16XNR; SOT95P230X110-3N
R_MOSFET: ERA-8AEB331V; RESC3216X70N
R_SWITCH: ERA-8AEB331V; RESC3216X70N
T5, T6: MCP9808T-E/MS; SOP65P490X110-8N

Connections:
AIN0: CONEXION_B1.6, Q1.1 (G), R_MOSFET.1
GND: CONEXION_B1.2, CONEXION_B2.5, Q1.2 (S), R_MOSFET.2, R_SWITCH.1, T5.4 (GND), T5.6 (A1), T5.7 (A0), T6.4 (GND), T6.6 (A1)
INT0: CONEXION_B1.7, CONEXION_B2.2
NICROMO: Q1.3 (D)
OC1A: CONEXION_B1.5, CONEXION_B2.1
SCL: CONEXION_B1.3, CONEXION_B2.4, T5.2 (SCL), T6.2 (SCL)
SDA: CONEXION_B1.4, CONEXION_B2.3, T5.1 (SDA), T6.1 (SDA)
T0: CONEXION_B1.8, PINES_SWITCH.2, R_SWITCH.2
VCC: CONEXION_B1.1, CONEXION_B2.6, PINES_SWITCH.1, T5.5 (A2), T5.8 (VDD), T6.5 (A2), T6.7 (A0), T6.8 (VDD)



Board: 2 copper layers, 82.5 x 29.0 mm, 8 parts (2 on the bottom side), 8 nets.

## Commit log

2020-03-25 Initial files
    [Deploy_assembly.iam, SoportePlaca_SPEL_Rev.3.ipt, SoportePlaca_SPEL_Rev.3.stp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]
2020-04-06 DXF files
    [interstageV2-AOutLine_intgssbA-2(Low).dxf, interstageV2-BOutLine_intgssbB-2(Low).dxf]
2020-04-13 IS version with hole
    [HoldVersionIS.dxf]
2020-04-15 DXF Files modificados
    [HoleVersionIS.dxf, Lista de componentes.xlsx, interstageV2-AOutLine_intgssbA-2(Low).dxf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]
2020-05-18 Placas PCB
    [Golilla M1.6 .ipt, Lista de componentes.xlsx, Picoblade.ipt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]
2020-05-18 Placas PCB
    [interstage_A2.brd]
2020-05-19 Soportes para paneles
    [Lista de componentes.xlsx, Placa A1 con soporte.stp, Placa A2 con soporte.stp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]
2020-05-24 Ensamblaje placa
    [ATMEGA328P.ipt, Clock ABM3B.ipt, Condensador 100nF.ipt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]
2020-06-30 Mini placas
    [Conector 3 pines.ipt, Lista de componentes.xlsx, Pads Soldadura.ipt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]
2020-07-11 Presentacion II
    [Placa A.dxf, Placa A2 smd.stp, Placa A2 tht.stp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]
2020-08-17 Gerber V3
    [copper_bottom.gbr, copper_top.gbr, drills.xln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]
2020-08-22 Actualización
    [ATMEGA328P.0001.ipt, ATMEGA328P.ipt, Clock ABM3.ipt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]

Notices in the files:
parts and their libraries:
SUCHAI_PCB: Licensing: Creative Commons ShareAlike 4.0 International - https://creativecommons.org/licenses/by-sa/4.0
